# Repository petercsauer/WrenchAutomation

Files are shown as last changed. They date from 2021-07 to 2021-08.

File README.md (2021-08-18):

# Bionic Wrench Manufacturing Automation
This is the repository for my final project in the MSR (Masters of Science in Robotics) program at Northwestern University. The project was to automate the production of the LoggerHead Tools Bionic Wrench.

## Overview

The goal for this project was to continue to evolve the design created by Levi Todes (MSR '18) and add usability features like a magazine to store wrench jaws, a bowl descrambler to orient wrench jaws, and a movable platform for easy wrench placement. 

There were three main components to this project, the structure which was made out of sheet metal, the magazine which was 3D printed and the bowl descrambler ramp which was also 3D printed. Each one of these parts went through many iterations along the design process. All of the parts were designed using SolidWorks and most were printed on the Ultimaker 3.

A PIC32MX250F128B was used to control the system, along with a DRV8834 stepper controller from pololu (for stepper motor control). The MPLab SNAP was used as the programmer and the code was in C. 

- Insert Video

## Approach
Going into this project I knew there were three main areas that I wanted to target -- The wrench placement, jaw orientation process and jaw feeding process. 

The wrench placement process in the previous design required the user to take off a drive gear, place the wrench in a 3D printed holder and then reattatch the gear to the assembly using some magnetic latches as can be see on [Levi's Repository](https://github.com/LeTo37/Part_Placement_Automation_Project).

My new mechanism uses a hinge to allow the wrench to be placed on in a horizontal orientation and then moved into a vertical orientation by just flipping the whole mechanism up. This can be done with a stepper motor and lead screw, but ultimately it was decided that its easy enough to do by hand. 

For the jaw orientation process, there was not really any work already completed. For this I first used pieces of cardboard, metal and tape to try and knock the pieces off of the ramp that were in the wrong orientations. After getting an understanding of how to orient the pieces, I created a few 3D printed designs and tested them out until one worked. I then refined that design a few more times until the pieces would consistently drop in the correct orientation out of the bottom of the descrambler.

For the jaw feeding process I started by modifying Levi's electromagnet technique, which would use an electromagnet to pull the jaw into position and then shut it off, allowing the jaw to succumb to gravity and fall into place. Unfortunately, I found this method to be unreliable, so I switched to a more mechanical design. This second big design iteration used a rod on the bottom and a feeding mechanism on top to feed the pieces through a track and also control when they were allowed to fall out as well. The main issue with this design was that despite numerous design iterations, I couldn't get the pieces to feed without catching on the track walls and jamming up the system. For the final big design iteration, I decided to switch to a magazine type feeder that uses a vertical tube and a pushrod to feed out the pieces like a pez dispenser. This method worked far better than the others and allowed for easy integration with the bowl descrambler through a vertical tube.

## Mechanical Design
The mechanical design involved in this project was by far the most important, most complex and thus the most time consuming aspect of the project. As is the nature of design, it involved a lot of iterations as well as a few changes in approach that ultimately led to the final design. This final set up is shown below.

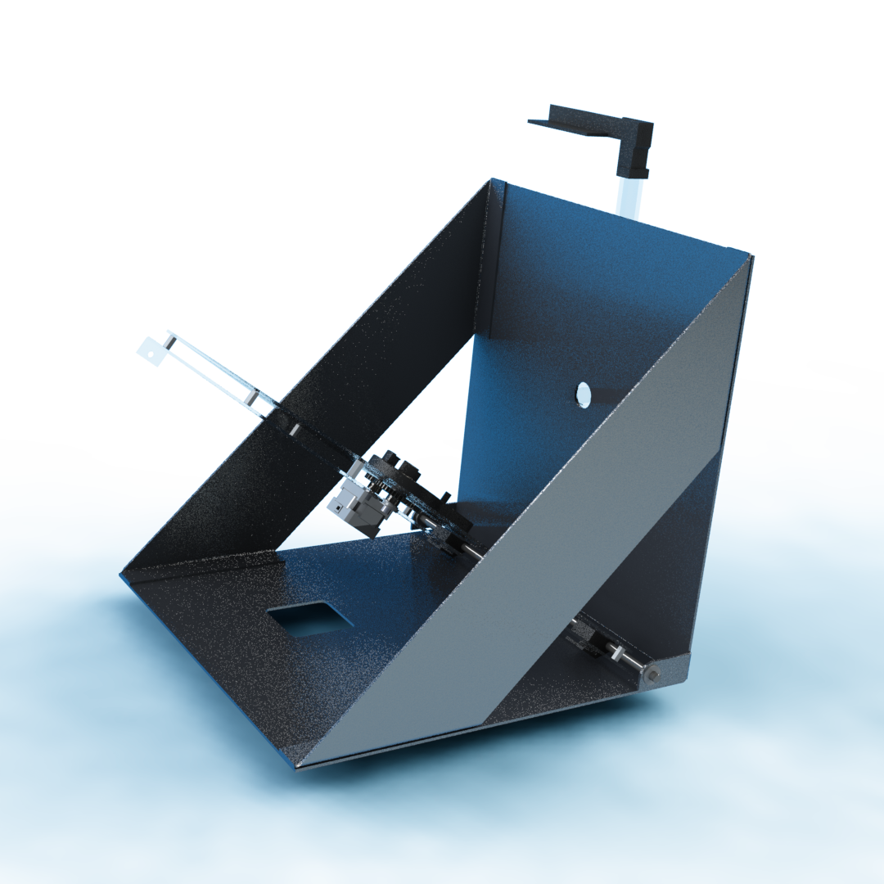
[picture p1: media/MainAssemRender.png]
Final


For more detailed descriptions of the mechanical design process please visit the [Mechanical Design Directory](/Mechanical_Design).

## Electronics

[This](/Electronics) directory contains the <a href="https://www.autodesk.com/products/eagle/overview" target="_blank">EAGLE CAD</a> files created by Levi for this project. It also contains a README with an updated picture of the final circuit.

## Code

The C code used to program the microcontroller is in [this](/Code). directory.

<!-- ## Future Work -->

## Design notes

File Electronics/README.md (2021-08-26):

# Electrical Design

This directory contains the eagle files that Levi created in his version of the device. My version did not modify his electronics besides the addition of a servo, the momentary addition of a second stepper motor and driver (which was later removed) and the removal of the electromagnet driver. 

## Microcontroller

For this project the [PIC32MX250F128B](../Docs/PIC32MX1XX2XX-28-36-44-PIN-DS60001168K.pdf) was used as the control unit for the process. It was used to control the stepper motor and servo and in the past was used to control an electromagnet, but ultimately it was decided to keep that on full time.

The breakout schematic from eagle for the process is shown below, which shows the 3.3V regulator, pololu dual h-bridge, micro usb connector (for power) and MPLAB SNAP (for programming). 

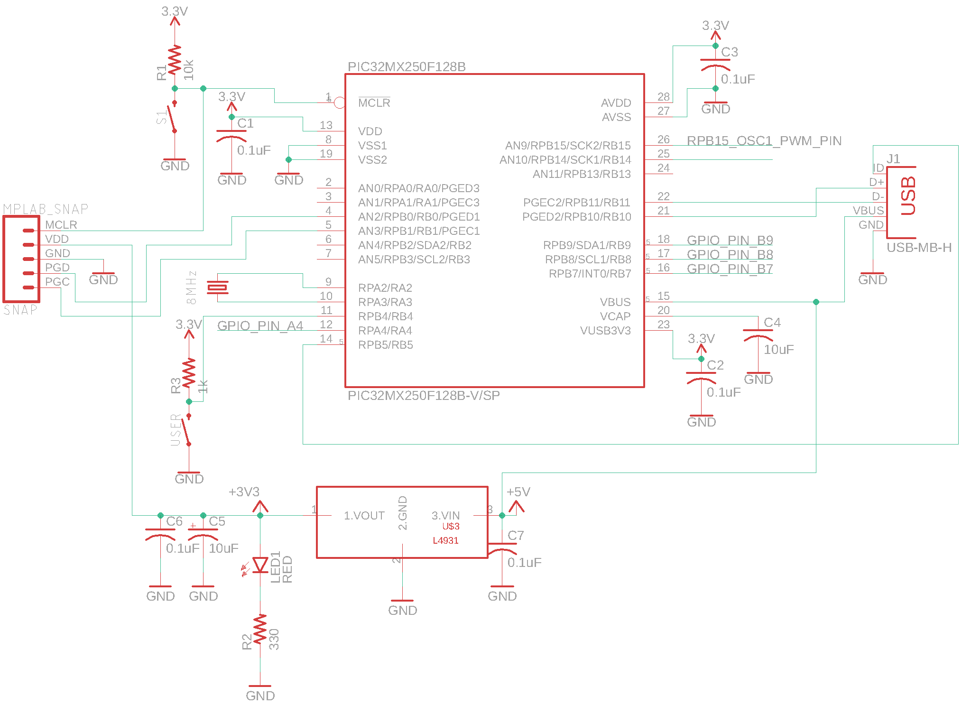
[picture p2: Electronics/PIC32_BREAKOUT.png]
PIC32_BREAKOUT


## Stepper Motor Driver

The circuitry used to control the stepper motor is the Pololu [MD20b](https://www.pololu.com/product/2133/resources) chip. This chip is a breakout board for the [DRV8825](../Docs/drv8825.pdf) which has two H-bridge
drivers and a microstepping indexer, along with some protective circuitry. This chip allows the stepper to be simply controlled by 3 GPIO pins to control the step resolution (M0,M1,M2) and one pin set to output a PWM signal (STEP). This chip also allows for 3.3V logic to be used from the microcontroller while supplying the motor with the 12V necesarry to use it. 

As can be seen in the [code](../Code) directory, pins M0, M1 and M2 are used to set the resolution at which the motor is controlled. Setting M0 and M1 high and M2 low sets the driver to control the motor in 1/8 step mode, meaning the 200-step-per-revolution motor now has 1600 microsteps per revolution. A PWM signal is sent to the STEP pin to drive the motor.

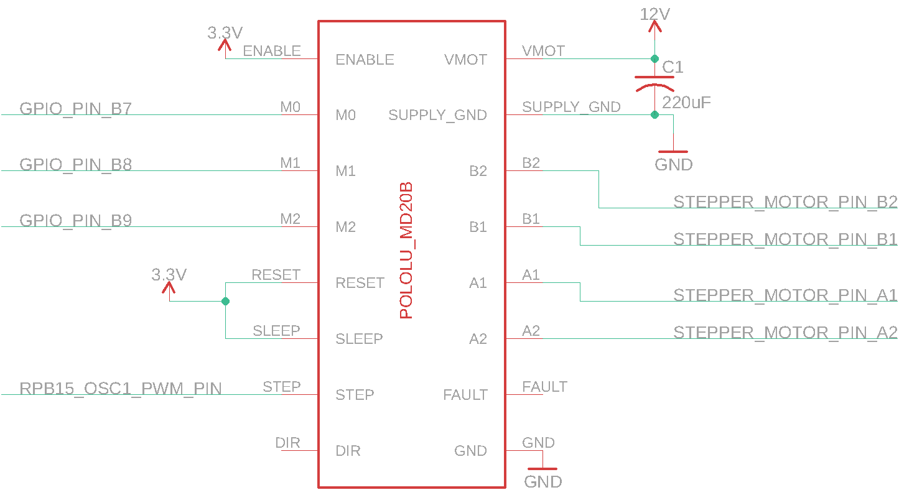
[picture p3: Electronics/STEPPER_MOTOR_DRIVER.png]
STEPPER_MOTOR_DRIVER


## Servo

A servo was added to the electronics part of this project. The servo had three wires, red, black and white which were connected to 5V, GND and pin 6 on the PIC32, respectively. A PWM signal was outputted to pin 6 which allows for control over the servo position. 

## Overall Layout

Here is a picture of the final layout of the system on it's breadboards. The smaller breadboard is running off of 12V (from an external supply) and the larger one runs off of USB which is converted to 3.3V by the Pololu voltage regulator you can see in the top center.
STEPPER_MOTOR_DRIVER

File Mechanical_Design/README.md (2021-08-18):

# Mechanical Design
The mechanical design part of this project was by far the hardest part. Many of the parts designed has complex geometries that required 11 hour + 3D print jobs per part. Because of this, a lot of analysis was done between part iterations to reduce "downtime" where I could not further refine the design. Although only a few key design iterations will be shown in this document, many smaller iterations took place on each part to enusre that the process ran smoothly and efficiently. 

## Initial Designs
Because I was continuing work on another students' project, there were intial designs available for me to work off of. Right off the bat, I noticed two main areas of Levi's design that I wanted to improve upon and Professor Brown gave me one addition to make to the process as well. These three changes/additions became the backbone of my project and were:

- Overall Structure
- Feeding Mechanism
- Jaw Orientation.

## Design Refinements
### Overall Structure
At the start of the project I identified the structure as one of the main components that both wouldnt hold up to a manufacturing environment and could use some refinement to improve usability. Mainly, the old design was a little too flimsy (it was a prototype so this makes sense). To fix this issue, I came up with a new sheet metal pattern that I was able to cut out of aluminum using a waterjet and bend using a brake. It had relatively similar geometry to Levi's initial prototype, but the wrench would be placed on the inside, rather than the outside and the structure as a whole was bigger than the initial. Below is the new design, followed by a wrench holder mechanism further discussed below.

<p float="left">
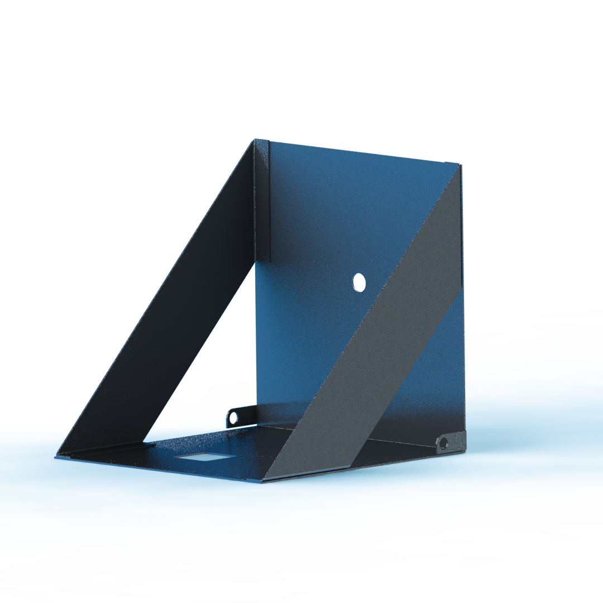
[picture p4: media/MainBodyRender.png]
  
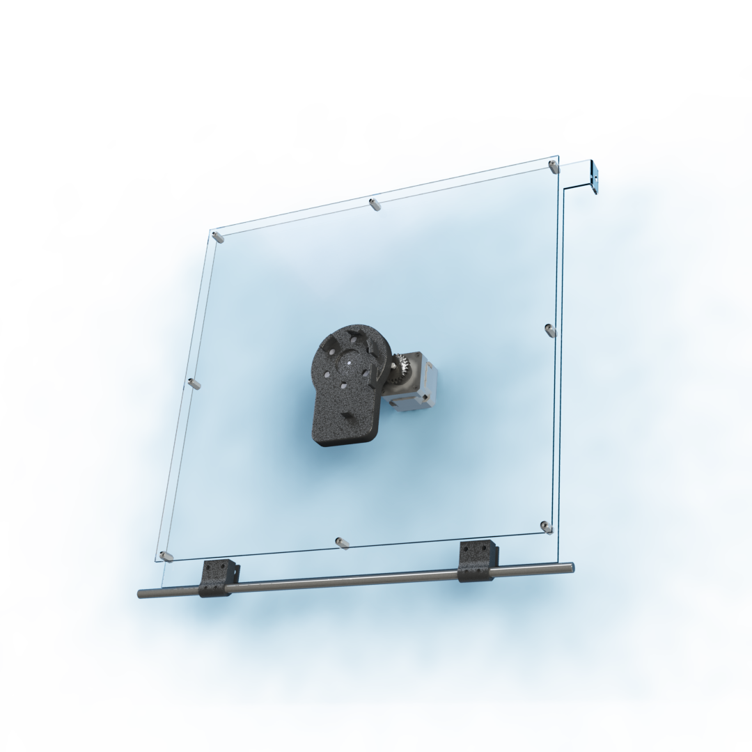
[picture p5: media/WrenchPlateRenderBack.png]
   
</p>

The new structure also has an important addition for usability. There is a middle panel that swings 90 degress from flat to vertical, allowing for easier wrench placement. The user can place the wrench in easily when it's in a horizontal mode and then the whole panel can be lifted up to interface with the jaw placement mechanism. Initially, this could be done using a stepper motor and lead screw, but ultimately it was decided that the user would be perfectly capable of doing this motion by hand so that was removed.

<p float="left">
  
</p>

Embedded in this platform is the mechanism that rotates the wrench 60 degrees for each different jaw. This system is geared 2:1 so it has the required torque to rotate the wrench against gravity in its vertical position. 

### Feeding Mechanism
The jaw feeding mechanism was the second design refinement I chose to tackle. Levi's design used an electromagnet to pull jaws one by one through a 3D printed tube, and then cut off power to the electromagnet allowing the jaw to fall into place in the wrench. I ultimately discovered that the electromagnet was too unreliable to continue to be used. It ended up being a passive drive to get the jaws into position so that they could be attracted by the electromagnet as well. 

I tried using the electromagnet in an initial design and found that it wasn't strong enough to reliably pull jaws to the correct positon. I tried different electromagnets as well and even tried building my own to the specs I wanted, but none worked reliably. 

I decided that I wanted a driven mechanism for getting the jaws into position, and that I wanted to rely less on the electromagnet. My inital design for this iteration was a feeder wheel driven by a continuous servo on the top of the jaws that would use friction to push the jaws through, and a "droprod" on the botton that could be pulled back by a second regular servo. The drop rod part of this iteration worked really well, but the feeder wheel had many issues. As the jaws went under the wheel, one edge would tweak up, causing the chute to become jammed and not let any other jaws through. I made a few different iterations of this design with tighter tolerances to try and prevent this behavior, but it just didn't end up working right.

For the final major design iteration on the feeding mechanism I realized that the wrench jaws were almost the same size and shape as a pez. I used a pez dispenser as inspiration and created a magazine style feeding mechanism that used a rod driven by a servo to push evenly on the whole back side of the jaw. This prevented any of the tweaking motion that jammed up the previous design. It also reduced the number of servos required by one. 

<p float="left">
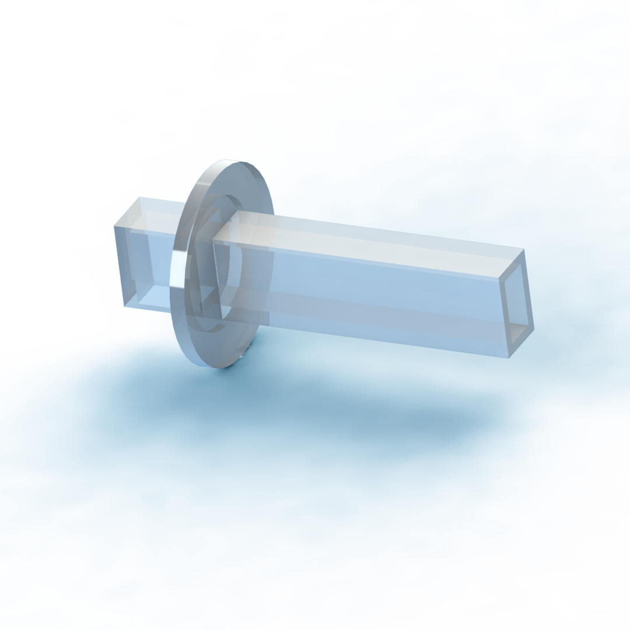
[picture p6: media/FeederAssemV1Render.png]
  
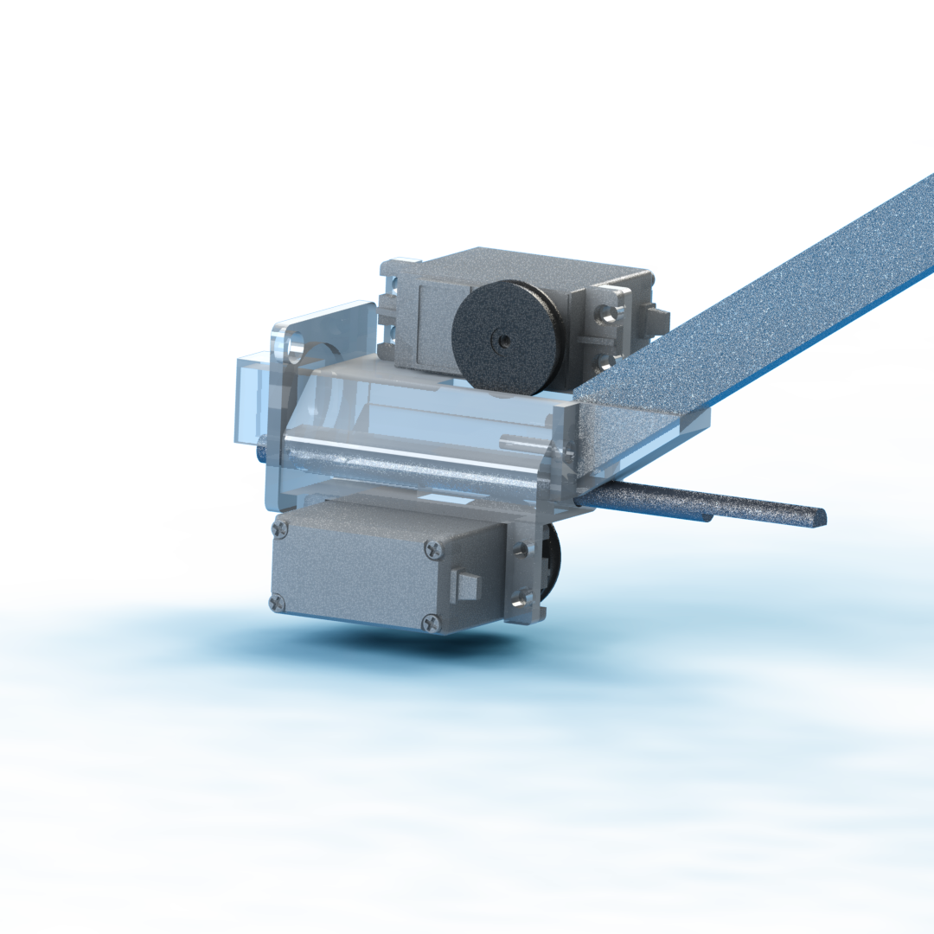
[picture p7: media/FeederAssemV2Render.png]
   
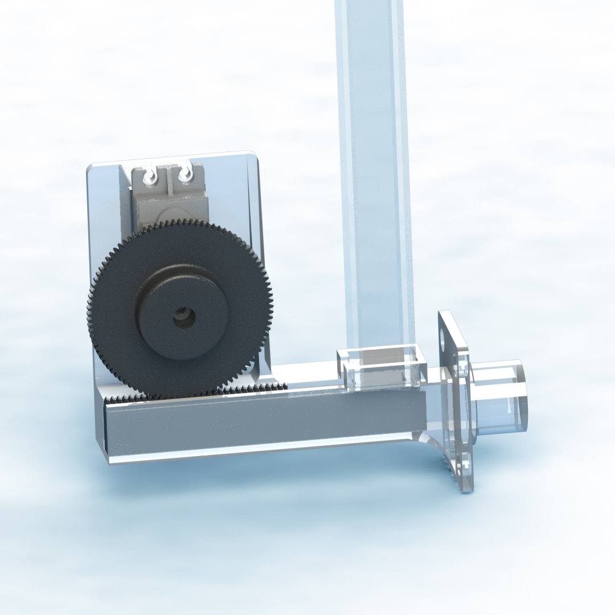
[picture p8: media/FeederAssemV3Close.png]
   
</p>
Left to Right - Electromagnet Design, Feeder Wheel Design, Magazine Design

### Jaw Orientation
This objective was given to me by Professor Brown, with the goal of being able to dump jaws into a bowl descrambler and have them load directly into the jaw feeder in the correct orientation. A bowl descrambler vibrates enough to drive jaws up a ramp and they get knocked off at different points along the way if they arent in the correct orientation. For this part of the project, I spent a good deal of time getting familiar with the technology by placing cardboard and metal knockoff pieces using tape. 

Eventually I understood enough about what would knock the pieces off to 3D print a design to attempt it. After a few revisions of this part, I was able to get the pieces consitently coming out of the machine in the correct orientation, running along a rail.

The next step was to design a was for them to drop off the rail I had them running along into the vertical "pez dispenser" chute. This also took a few design iterations but eventually I ended up with this part, which interfaces at the end of the path on the bowl descrambler and at the top of the pez dispenser tube.

<p float="left">
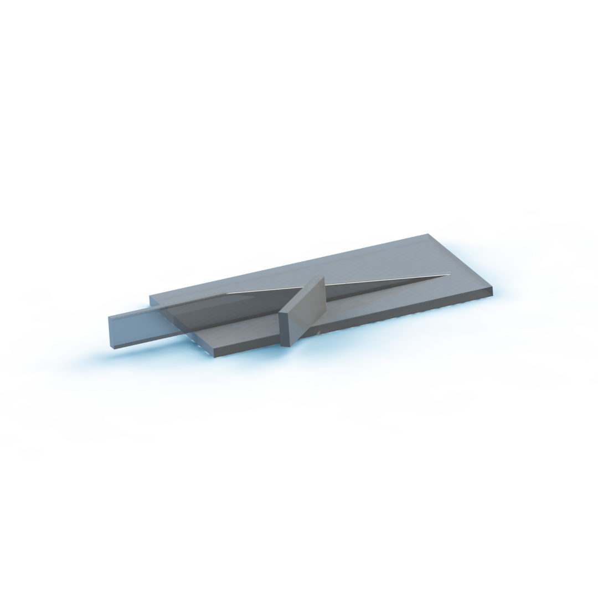
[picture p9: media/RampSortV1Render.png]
    
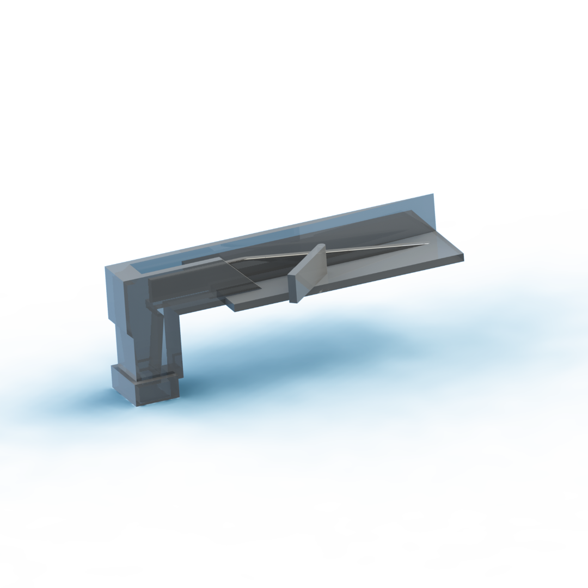
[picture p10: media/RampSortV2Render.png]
  
</p>

The angled wall knocks off all pieces that arent in a vertical orientation, and the sloped rail forces pieces that arent in the correct vertical orientation into a horizontal one, which causes them to get knocked off by the angled wall. The second longer wall with a slope at the end directs the pieces into the correct position to get picked up by the sloped rail. At the end, the box looking section is a funnel that funnels the pieces into a vertical magazine tube.

## Other components

### Actuators
A second stepper motor and drive board were added to drive the leadscrew and pull the platform to vertical, but those were since removed because it was decided to be unnecessary. A servo was also added that drives the rack for the magazine feeder design. 

### Electromagnet
An electromagnet was still used to hold the jaws in places as the platform is lowered to its horizontal position. Without the electromagnet, the jaws at the top of the wrench would fall out due to gravity on the way down. The electromagnet is embedded in the 3D printed wrench holder and is constantly on (run at 12V). However in the most recent version the electromagnet was swapped for 6 smaller neodymium magnets -- mainly because the electromagnet was always on and its wires would constantly get tangled.

### Wrench Holder
The wrench holder also went through a few design iterations. Starting out with Levi's inital design, I hollowed out the back to make room for the electromagnet and simplified the design a little bit because some of the additional features from his original were no longer necessary with my new design. 

<p float="left">
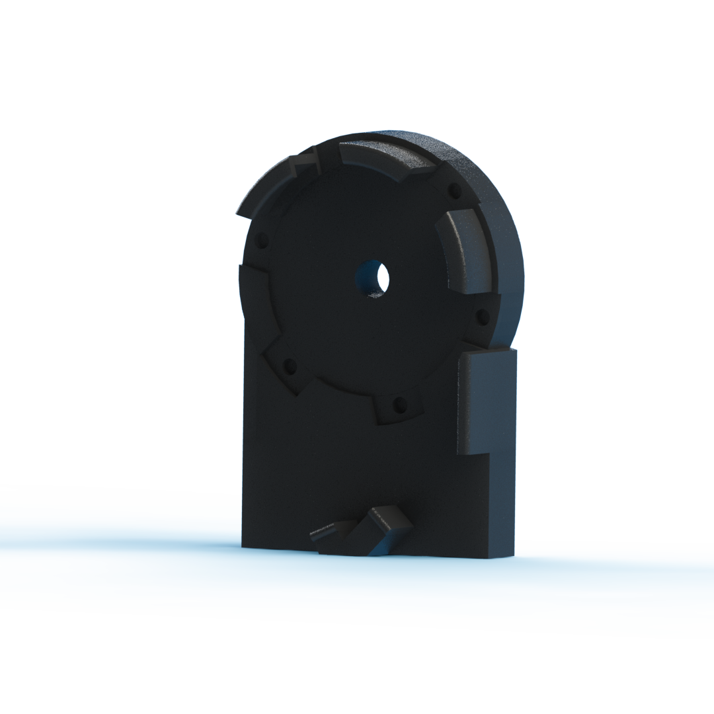
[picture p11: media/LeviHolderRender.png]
  
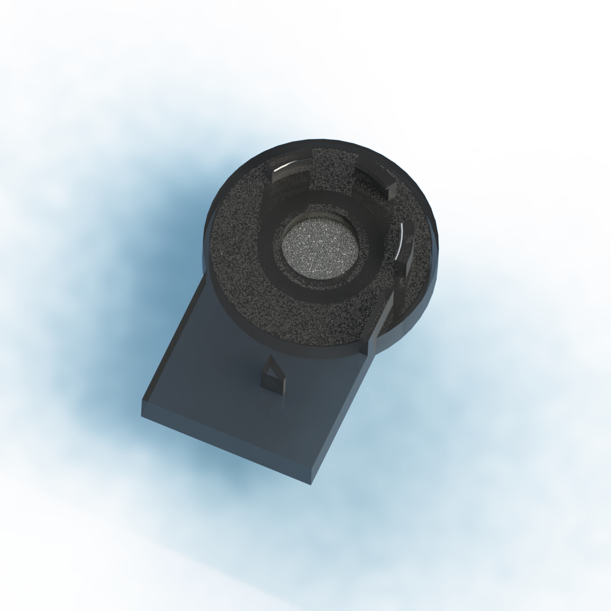
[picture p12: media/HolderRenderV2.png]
   
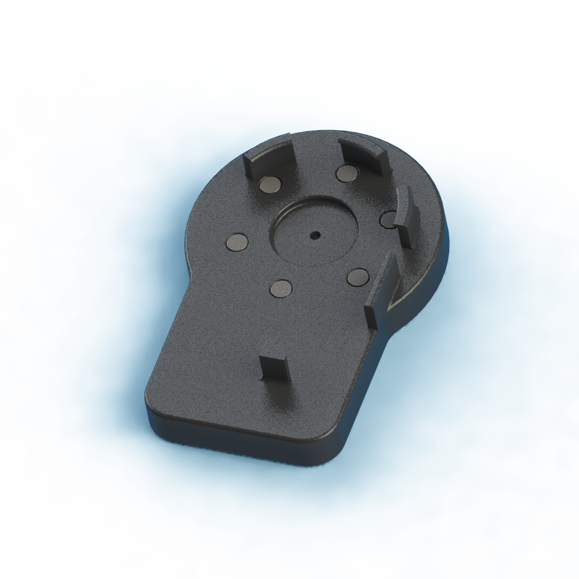
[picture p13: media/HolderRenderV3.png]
   
</p>

In the final design iteration for this part, I used 6 neodymium magnets instead of the electromagnet to improve reliability and get rid of the wires coming off of the electromagnet which would often get tangled.

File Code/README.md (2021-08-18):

# Code

The [MPLAB X IDE](https://www.microchip.com/mplab/mplab-x-ide) was used in this project to program the [PIC32MX250F128B](../Docs/PIC32MX1XX2XX-28-36-44-PIN-DS60001168K.pdf) microcontoller. Code was written in C and programmed using the MPLab SNAP.

The code for this project is relatively straightforward with two main functions. One function is control of the servo by varying the PWM output on pin 6 of the PIC32. By changing the PWM, the servo will go to different positions. The other function is for movement of the stepper motor. This is done again through PWM. There are also four additional wires going to the Pololu DRV8834 board, three of which control microstepping and the last controls direction.

Overall, the code activates a 6X loop when a limit switch is pressed and each time it goes through the loop the wrench moves 60 degrees, the feeder pushes out a new jaw and the wrench wiggles twice to attempt to ensure that the jaws fall back into place. At the end of the loop, the mechanism swings back around 360 degrees in the opposite direction to get back to 0.

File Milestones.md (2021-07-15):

# Spring Quarter Milestones:

* Decision about bowl decramblers/feeders - Assess different feeders for feed rate, ability to handle small pieces, how pieces can be presented after descrambling, size, cost.
	-- maybe order them before end of the quarter (ask Prof. Brown). Quarter ends June 8

* 3D print and laser cut prototype parts - Thursday 23 May

* Experiment on different "arm" choices - such as magnetic, suction, normal gripper.  - Tuesday/Thursday 28/30 May

* Before June 8, have a prototype/design idea for placement of jaws in wrench - rotate wrench or rotate arm.

# Fall Quarter Milestones:

* Go into Fall quarter with plan to build design from Spring Quarter.

* Intitial Steps to fabricate the design - metal wor in the shop - 1st/2nd week

* Construct and put together mechatronic functionality of design - 3rd/4th week

* Integrate design parts to have functioning system

* Optimise design to its peak ability

* End Goal - fully automated system for placing jaws. Available to implement in manufacturing line

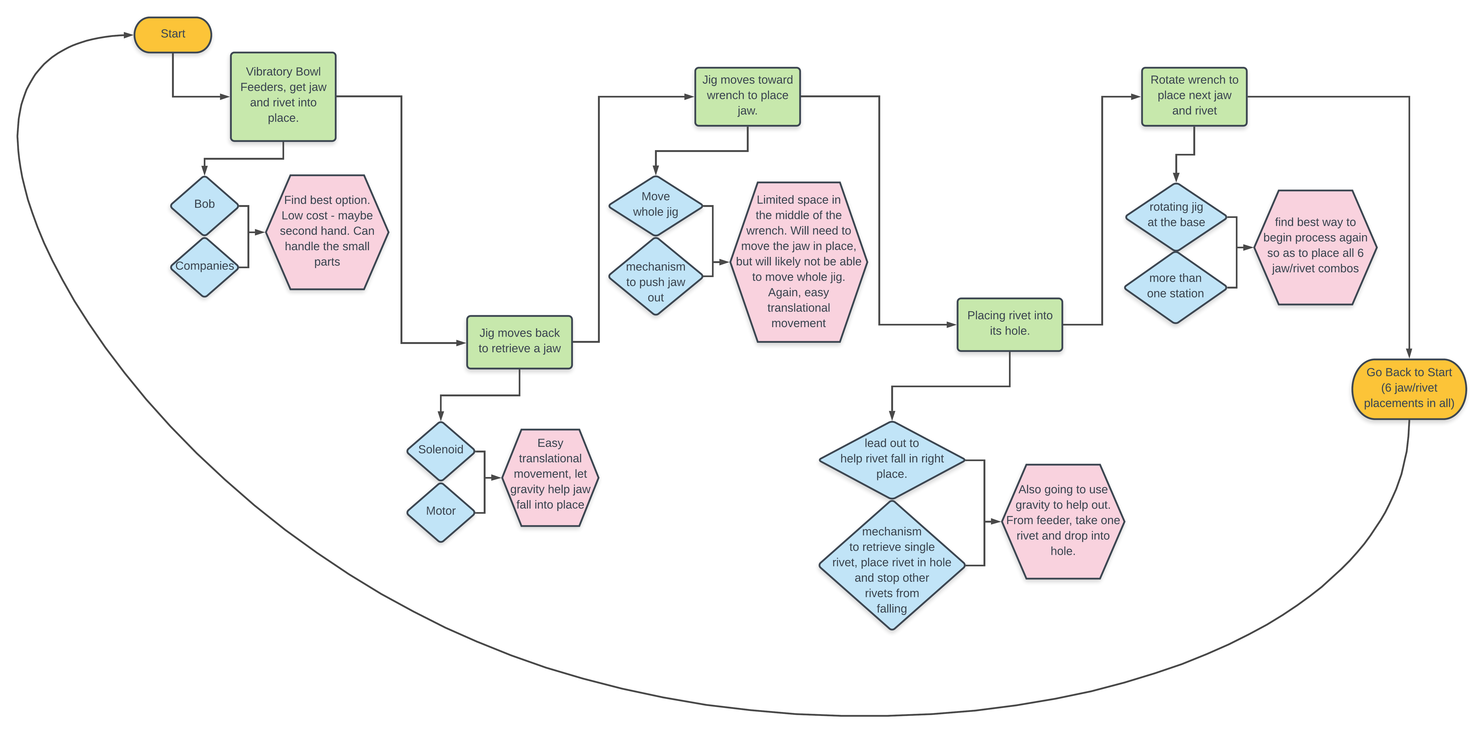
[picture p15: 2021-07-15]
media/Wrench_Journey_Map.png

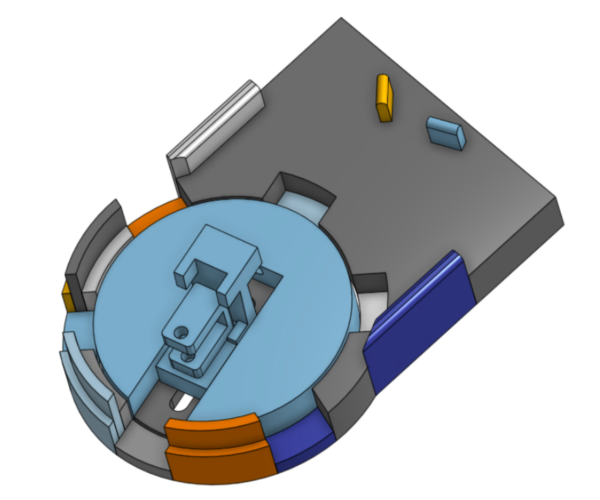
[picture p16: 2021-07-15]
media/Feed_from_top.png

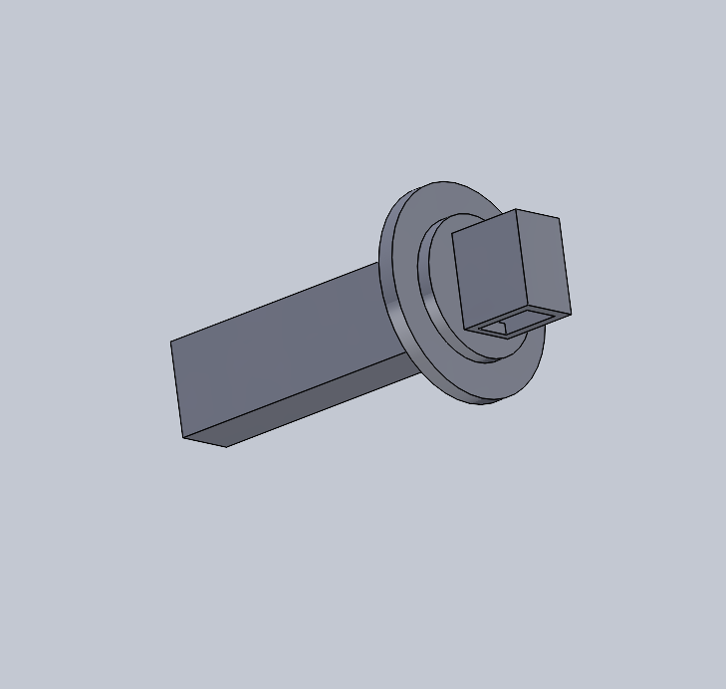
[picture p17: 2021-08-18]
media/FeederAssemV1.PNG

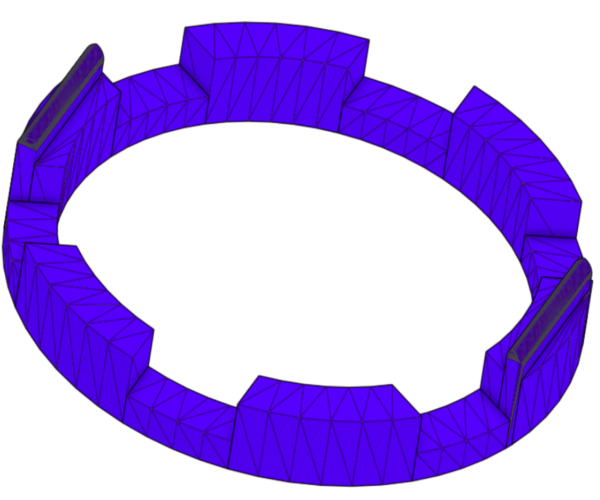
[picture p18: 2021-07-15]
media/wrench_outer_jig_II.png

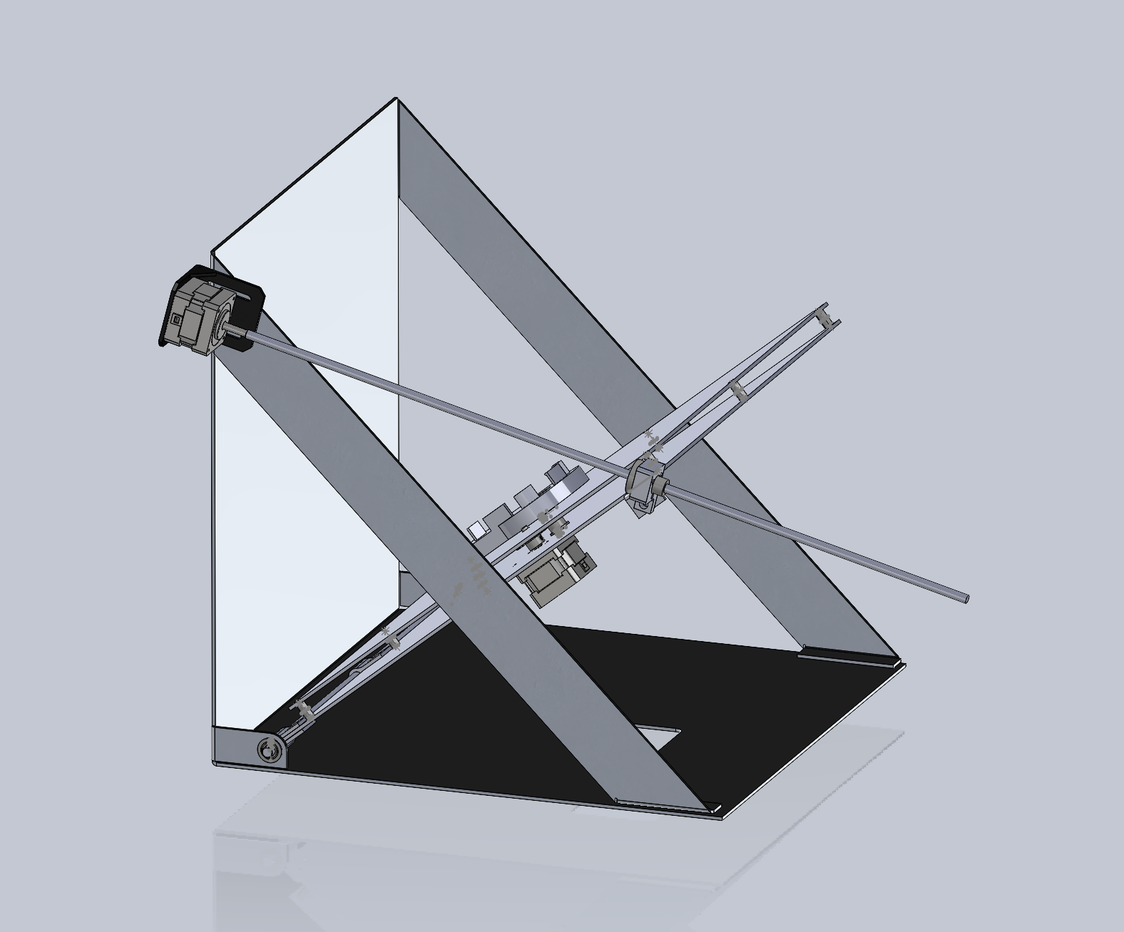
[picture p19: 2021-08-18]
media/SideAngle3.PNG

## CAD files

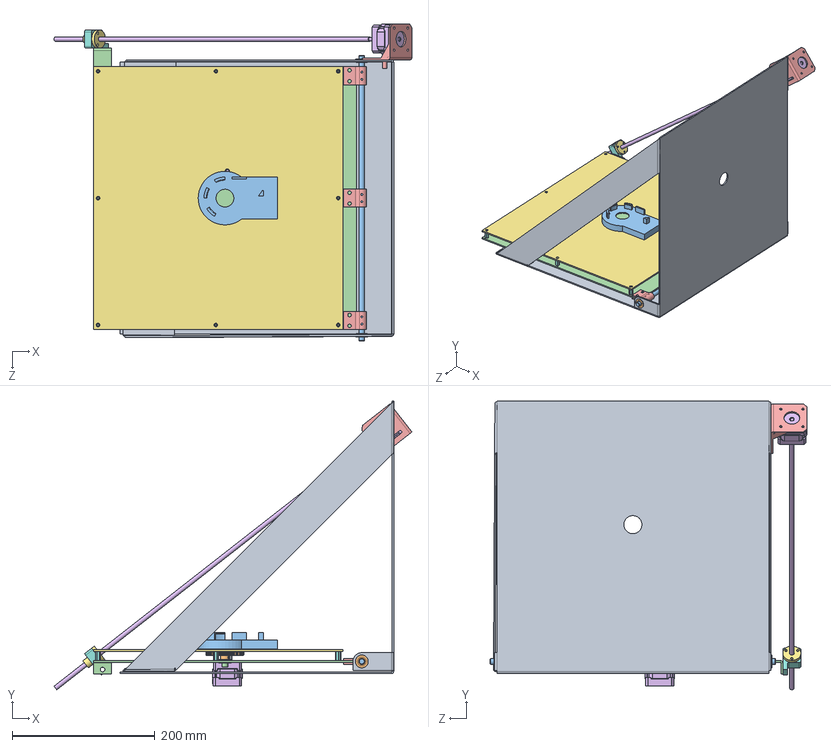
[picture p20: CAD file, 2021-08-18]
Mechanical_Design/FullAssembly.SLDASM
501.6 x 404.4 x 443.8 mm
MainBody
8mmBallBearing x 4
8mmShaft
WrenchPlate
ShaftPanelHolder x 3
StepperMotorNEMA17 x 2
BackPlate
HexStandoff#6 x 8
StepperGearPitch241
StepperGearPitch24
WrenchHolderV2
Electromagnet
NEMA17 - Steel Motor Mount
LeadScrew
6350K166_ULTRA-PRECISION LEAD SCREW
LeadScrewAdapter

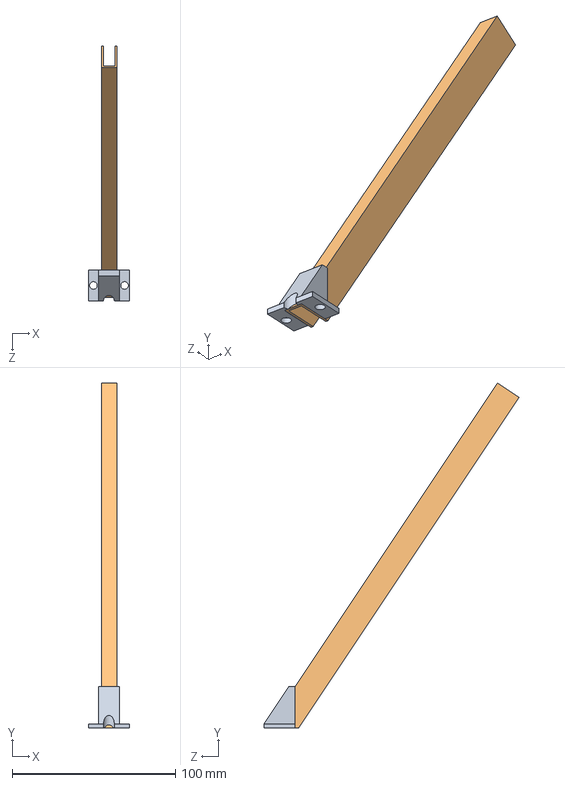
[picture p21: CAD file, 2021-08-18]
Mechanical_Design/Motion/ConnectBowlDescrambler.SLDASM
25.4 x 211.3 x 156.2 mm
RampHolder
JawTrack

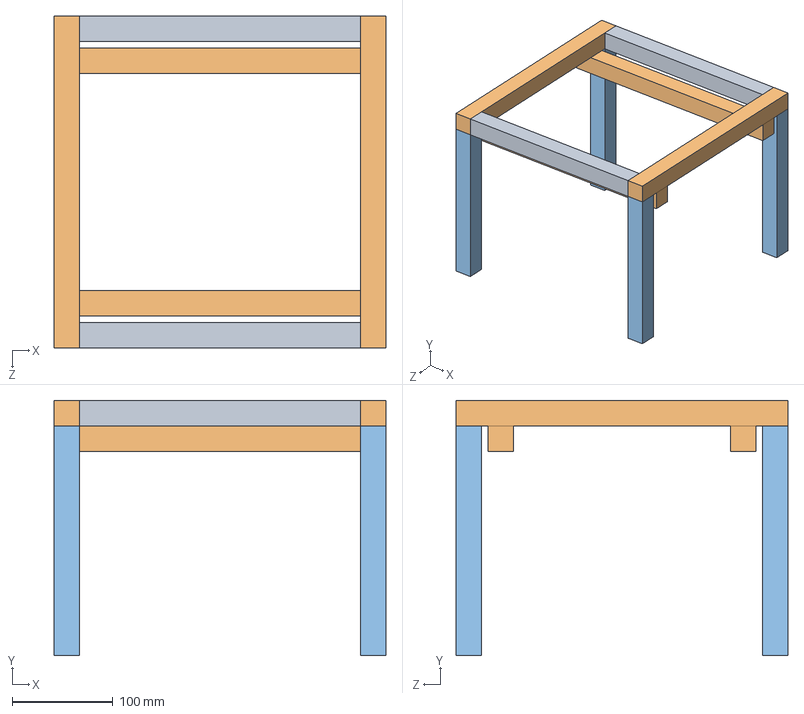
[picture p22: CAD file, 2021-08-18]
Mechanical_Design/Structure/Stand/BowlHolder.SLDASM
330.2 x 254.0 x 330.2 mm
9.5in x 2
11.5in x 4
9in x 4

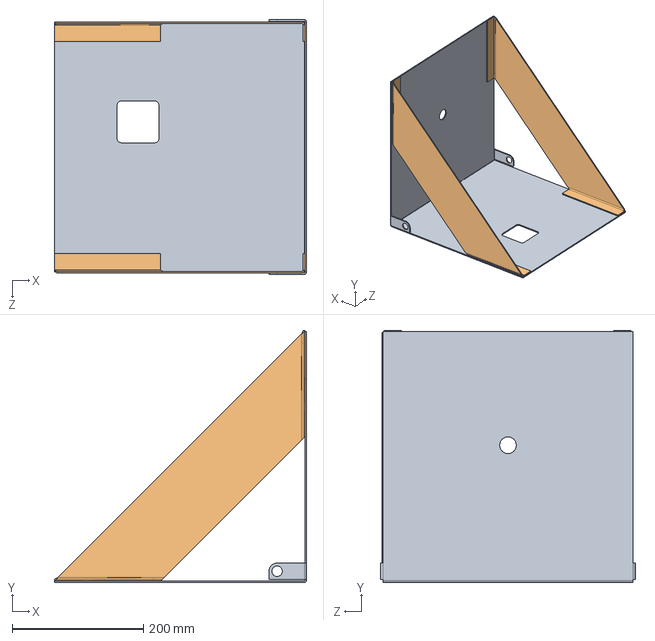
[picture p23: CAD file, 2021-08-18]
Mechanical_Design/FullAssemblyV2.SLDASM
383.5 x 383.5 x 387.6 mm
MainBody
DiagonalHolder x 2

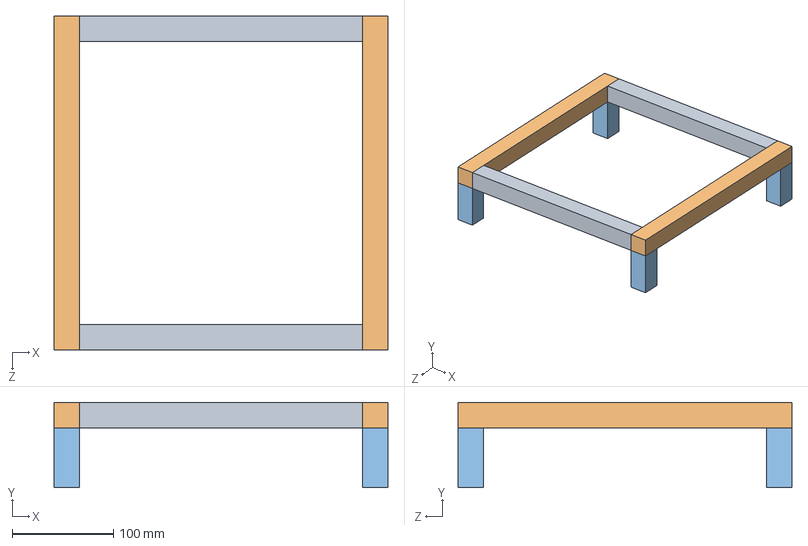
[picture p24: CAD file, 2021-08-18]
Mechanical_Design/Structure/Stand/MechanismHolder.SLDASM
330.2 x 84.3 x 330.2 mm
9.5in x 2
11.5in x 2
2.32in x 4

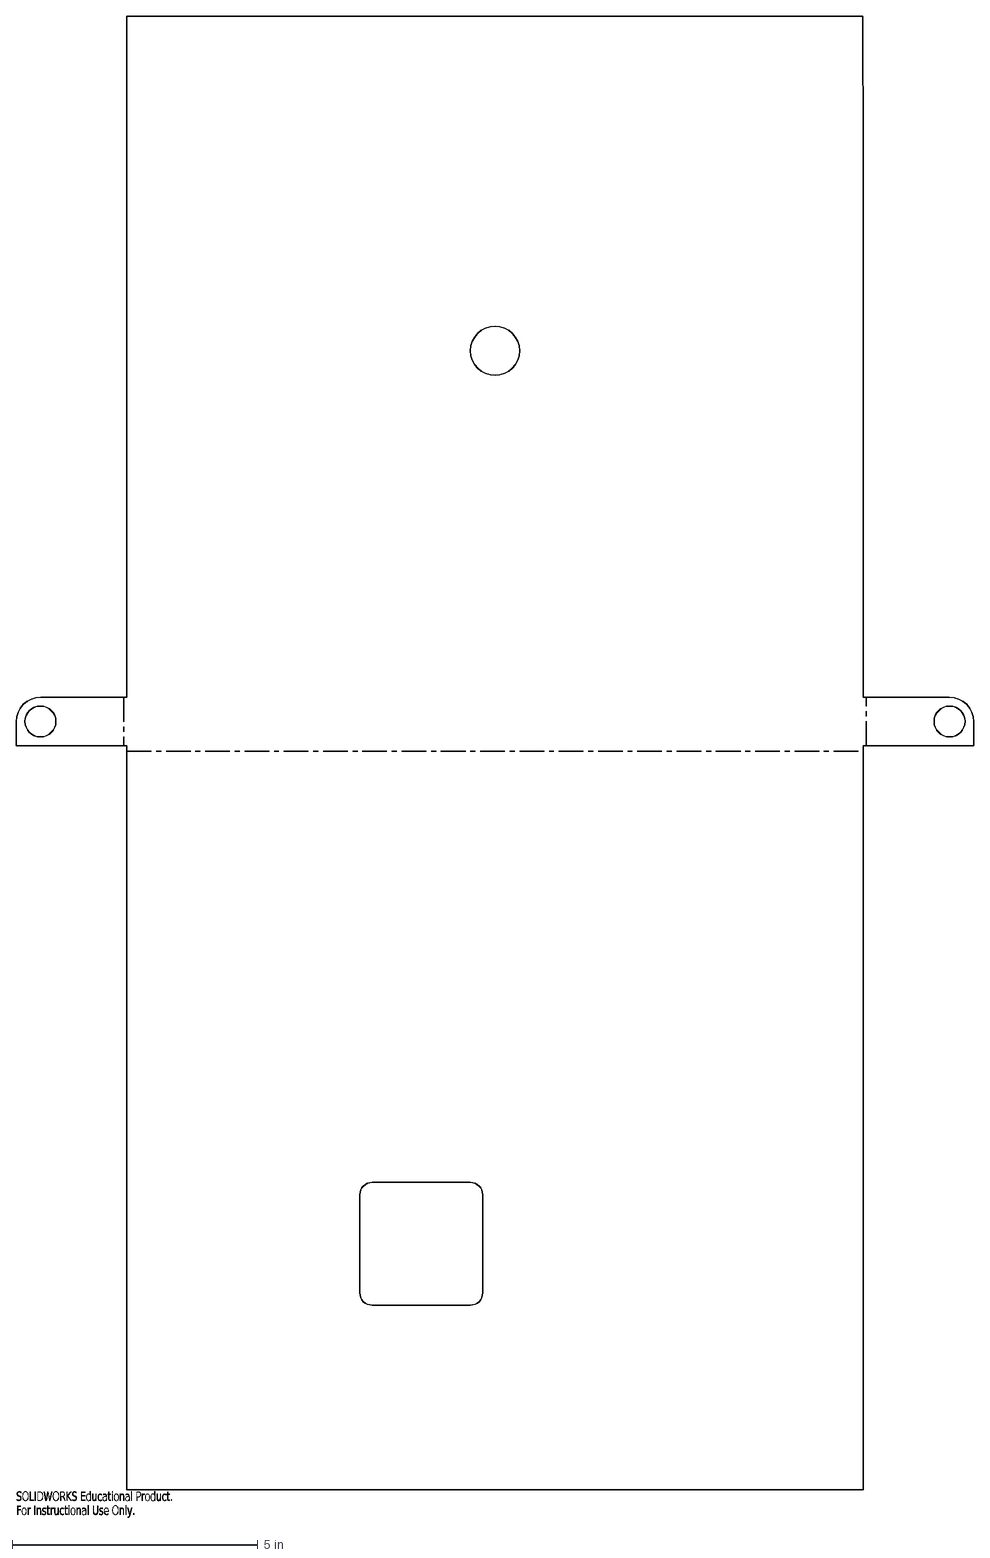
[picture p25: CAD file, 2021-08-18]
Mechanical_Design/Structure/MainBody2.DXF
SOLIDWORKS Educational Product.
For Instructional Use Only.

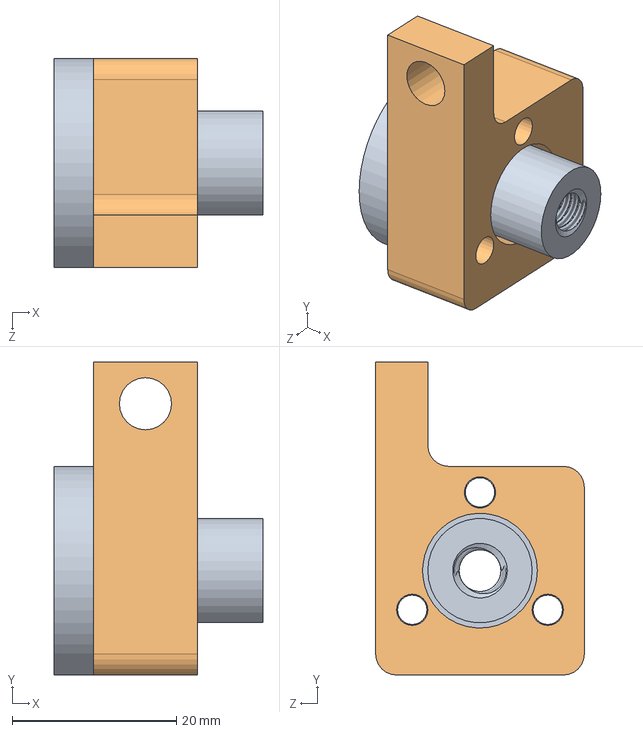
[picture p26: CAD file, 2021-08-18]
Mechanical_Design/Motion/Threaded Rod End.SLDASM
25.4 x 38.1 x 25.4 mm
6350K166_ULTRA-PRECISION LEAD SCREW
LeadScrewAdapter

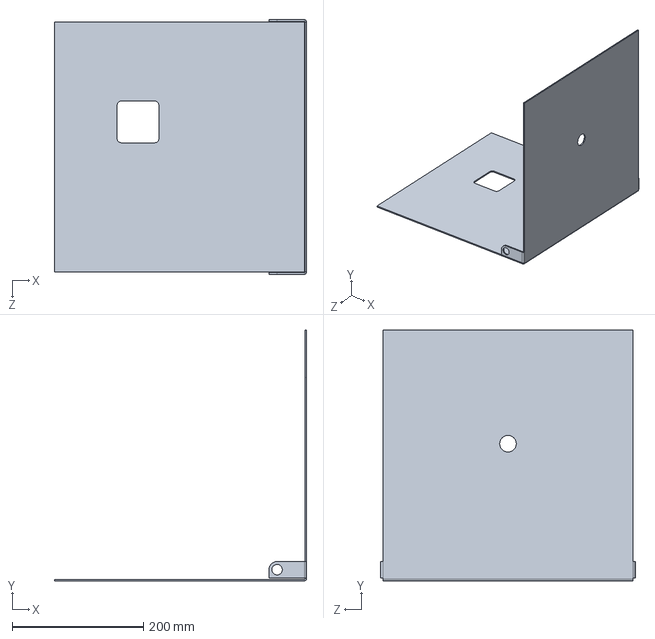
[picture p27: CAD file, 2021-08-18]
Mechanical_Design/Structure/MainBody.SLDPRT
383.5 x 381.9 x 387.6 mm

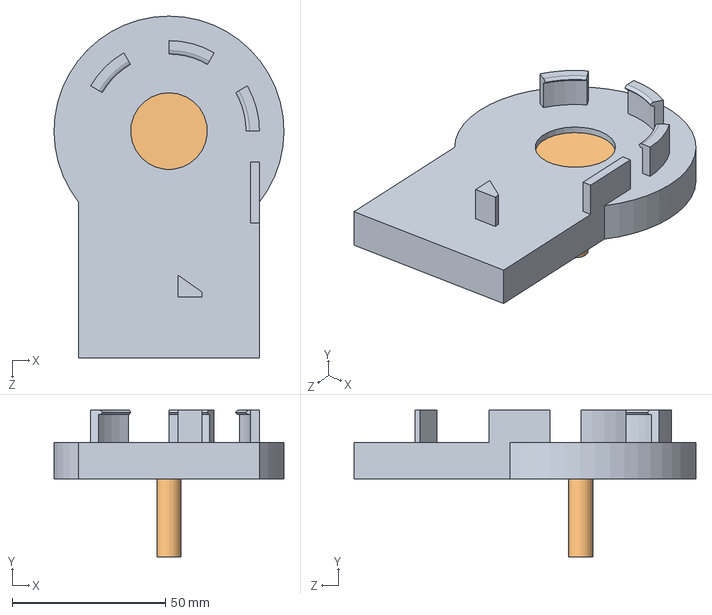
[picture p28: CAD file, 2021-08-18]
Mechanical_Design/Structure/WrenchHolderAssem.SLDASM
75.0 x 47.9 x 111.5 mm
WrenchHolderV2
Electromagnet

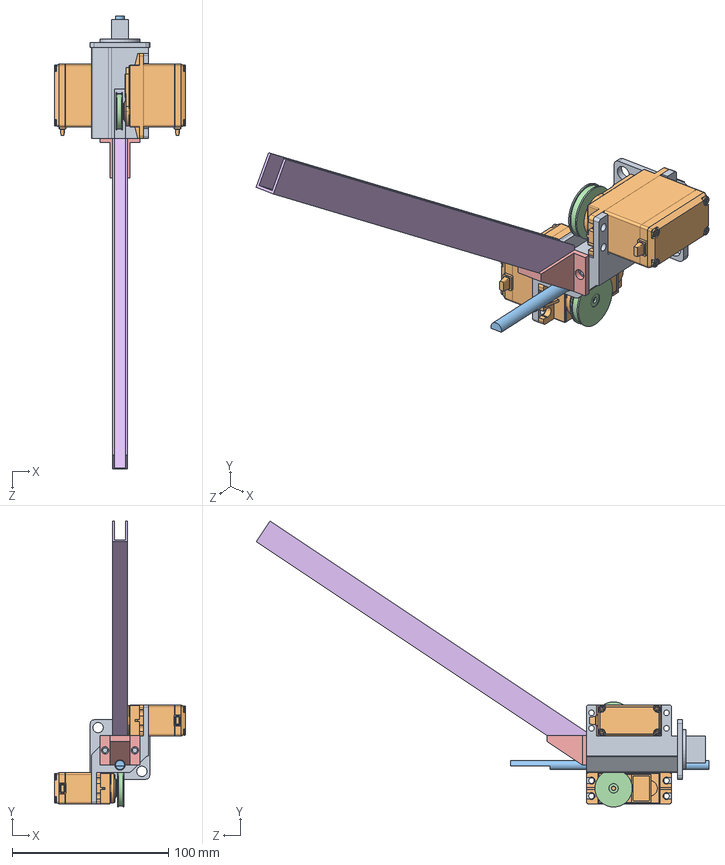
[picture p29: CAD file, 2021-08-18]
Mechanical_Design/Motion/FeederAssem.SLDASM
84.0 x 183.0 x 289.5 mm
JawFeederV3
FeederServo x 2
DropRod
DriverWheel x 2
RampHolder
JawTrack

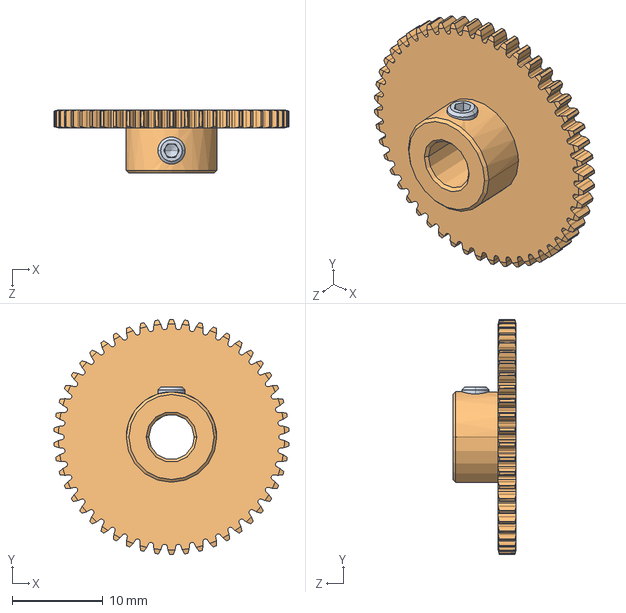
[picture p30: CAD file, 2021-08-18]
Mechanical_Design/Motion/StepperGear.SLDASM
26.0 x 26.0 x 7.00 mm
GEABB0_5_50_2_B_5_3
GEABB0_5_50_2_B_5_5

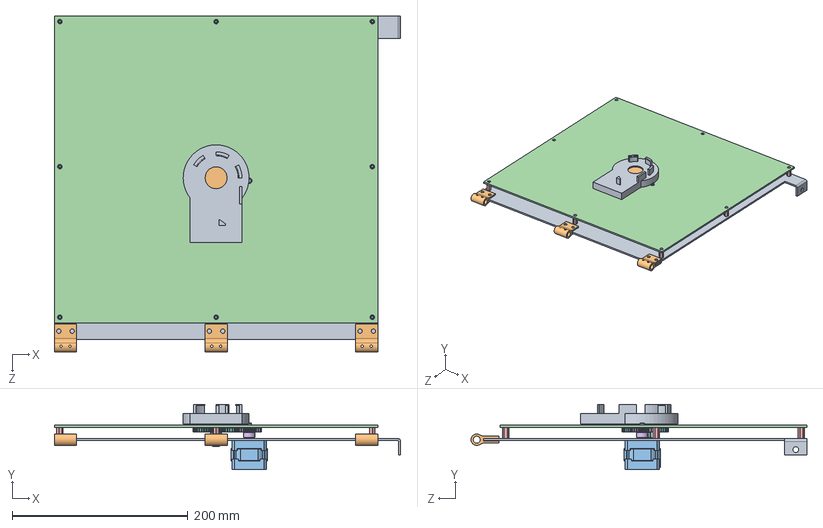
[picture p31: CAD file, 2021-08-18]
Mechanical_Design/Structure/WrenchPlateAssem.SLDASM
394.2 x 74.4 x 382.5 mm
WrenchPlate
ShaftPanelHolder x 3
StepperMotorNEMA17
BackPlate
HexStandoff#6 x 8
StepperGearPitch241
8mmBallBearing x 2
StepperGearPitch24
WrenchHolderV2
Electromagnet

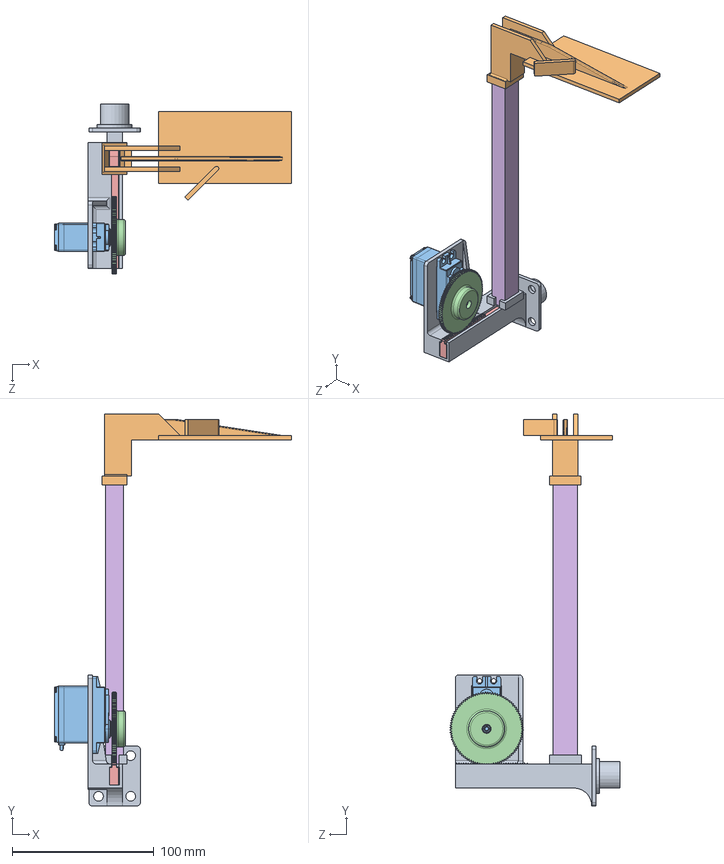
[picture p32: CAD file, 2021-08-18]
Mechanical_Design/Motion/FeederAssemV7.SLDASM
167.6 x 276.7 x 120.1 mm
JawFeederV7
RampSortV2
FeederServo
DriveGear
FeederPlungerV2
Chimney3DPrint

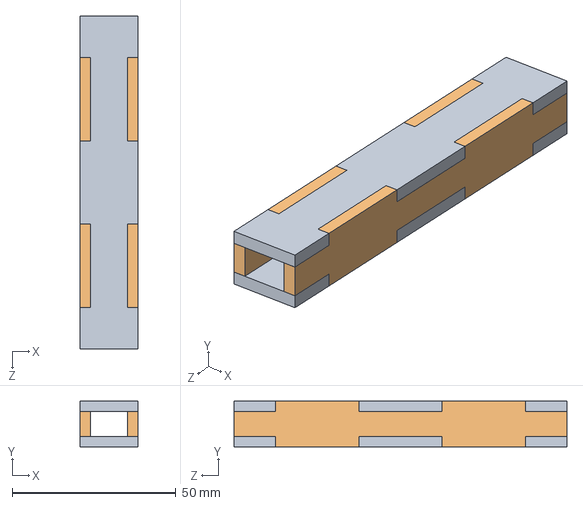
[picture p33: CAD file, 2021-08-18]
Mechanical_Design/Motion/ChimneyAcrylic.SLDASM
17.8 x 14.0 x 101.6 mm
ChimneyShort x 2
ChimneyLong x 2

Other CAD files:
Mechanical_Design/Structure/Flat-Pattern1 - MainBody.DXF
Mechanical_Design/Structure/MainBodyAssem.SLDASM
Mechanical_Design/Structure/Stand/9in.SLDPRT
Mechanical_Design/Motion/DriverWheelJaws2.SLDPRT
Mechanical_Design/LeadScrewAdapter.STL
Mechanical_Design/Motion/8mmBallBearing.SLDPRT
Mechanical_Design/Motion/8mmShaft.SLDPRT
Mechanical_Design/Motion/8mmShaftShort.SLDPRT
Mechanical_Design/Motion/BowlFeeder.SLDPRT
Mechanical_Design/Motion/ChimneyLong.DXF
Mechanical_Design/Motion/ChimneyLong.SLDPRT
Mechanical_Design/Motion/ChimneyShort.DXF
Mechanical_Design/Motion/ChimneyShort.SLDPRT
Mechanical_Design/Motion/DriveGear.SLDPRT
Mechanical_Design/Motion/DriveGear.STL
Mechanical_Design/Motion/DriveGearV2.STL
Mechanical_Design/Motion/DriverWheel.SLDPRT
Mechanical_Design/Motion/DriverWheel.STL
Mechanical_Design/Motion/DriverWheel2.STL
Mechanical_Design/Motion/DriverWheelJaws.SLDPRT
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

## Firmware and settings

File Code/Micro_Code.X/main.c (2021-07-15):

#include "Setup.h"      //PIC
#include "Stepper.h"    //STEPPER MOTOR
#include"PWM.h"         //PWM

#include <stdio.h>
#include <stdlib.h>
#include <math.h>

int main() {
    __builtin_disable_interrupts();
    // set the CP0 CONFIG register to indicate that kseg0 is cacheable (0x3)
    __builtin_mtc0(_CP0_CONFIG, _CP0_CONFIG_SELECT, 0xa4210583);
    // 0 data RAM access wait states
    BMXCONbits.BMXWSDRM = 0x0;
    // enable multi vector interrupts
    INTCONbits.MVEC = 0x1;
    // disable JTAG to get pins back
    DDPCONbits.JTAGEN = 0;
    //Make B4 and B2 an input (USER)
    TRISBbits.TRISB4 = 1;
    TRISBbits.TRISB3 = 1;
    //Make A4 an output (ELECMAGNET)
    TRISAbits.TRISA4 = 0;
    //Stepper Motor Setup (and PWM)
    Stepper_Setup();
    PWM_init();
    __builtin_enable_interrupts();

    LATAbits.LATA4 = 1;
    _CP0_SET_COUNT(0);

    //    Step_60();
    int trig = 0;
    int prev = 1;
    int dir = 1;
    int counter = 0;
    while (1) {

        if (prev == 0){
            Stop();
            int i = 0;
            while (i<6){ 
                Step_60(0);
                _CP0_SET_COUNT(0);
                while (_CP0_GET_COUNT() < 15000000) {
                }
                i++;
            }
            i = 0;
            while (i<6){ 
                Step_60(1);
                i++;
            }
            Step_Back(0);
            prev = 1;
        }else{
            prev = PORTBbits.RB4;
            Step(1);
        }






    }

}

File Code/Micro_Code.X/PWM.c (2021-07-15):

#include"PWM.h"

void PWM_init(void) {
    //Open pins for OC1 and OC3
    RPB15Rbits.RPB15R = 0b0101; //Set B15 as OC1 (PIN 2)
    RPB14Rbits.RPB14R = 0b0101; //Set B14 as OC3 (PIN 2)


    //***************TIMER 3 PWM********************
    T3CONbits.TCKPS = 0; //Prescaler N=1
    // period = (PR3+1) * N * 20.83 ns
    PR3 = 47999; //With prescaler of 1 give a 1 kHz signal
    TMR3 = 0; //reset the timer  
    T3CONbits.ON = 1; //Turn on the timer
    //********************
    
    //***************TIMER 2 PWM********************
    T2CONbits.TCKPS = 0; //Prescaler N=1
    // period = (PR3+1) * N * 20.83 ns
    PR2 = 47999; //With prescaler of 1 give a 1 kHz signal
    TMR2 = 0; //reset the timer  
    T2CONbits.ON = 1; //Turn on the timer
    //********************
    
    //OC3
    OC3CONbits.OCM = 0b110; //PWM mode without fault pin; other OC3CON bits are defaults
    OC3RS = 0; //0% duty Cycle
    OC3R = 0; //0% duty Cycle
    OC3CONbits.OCTSEL = 0; //Use timer 2
    OC3CONbits.ON = 1; // turn on OC3

    //OC1
    OC1CONbits.OCM = 0b110; //PWM mode without fault pin; other OC1CON bits are defaults
    OC1RS = 0; //0% duty Cycle
    OC1R = 0; //0% duty Cycle
    OC1CONbits.OCTSEL = 1; //Use timer 3
    OC1CONbits.ON = 1; // turn on OC1

}

void setDuty(float percent) //0 = forward, 1 = back
{
    int duty;
    percent = percent / 100;
    duty = (int) (percent * 2400);
    
    OC1RS = duty;

}

void setDutyWrench(float percent) //0 = forward, 1 = back
{
    int duty;
    percent = percent / 100;
    duty = (int) (percent * 2400);

    OC3RS = duty;

}
